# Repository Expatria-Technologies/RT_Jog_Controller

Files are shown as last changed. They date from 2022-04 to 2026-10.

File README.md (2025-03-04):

flag

# Elbows up.

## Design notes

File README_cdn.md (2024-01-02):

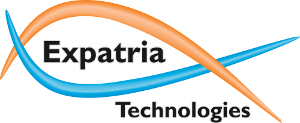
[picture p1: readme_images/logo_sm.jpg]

# Jog2K Jog Controller for GRBLHAL2000 and Flexi-HAL
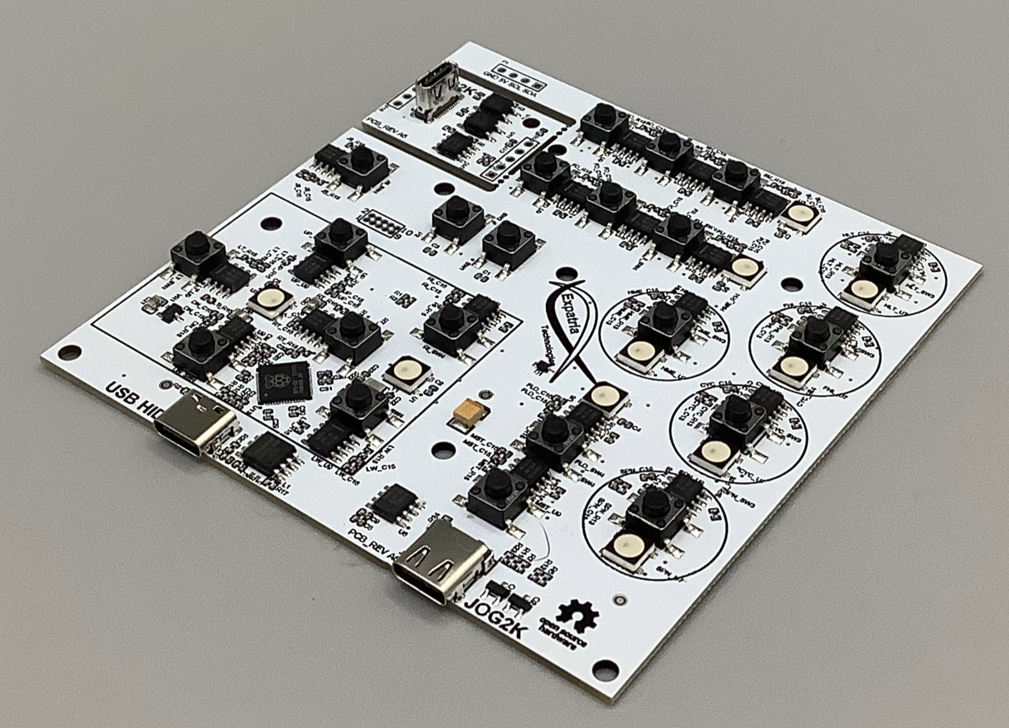
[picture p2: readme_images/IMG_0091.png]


Expatria Technologies jog controller for GRBLHAL2000 and Flexi-HAL boards

Assembled PCBs currently available in our online store:

https://expatria.myshopify.com/products/jog2k-keypad-pendant-pcba

Please consider buying a board to support our open-source designs.

This jog controller was developed for the GRLBHAL20000 and Flexi-HAL boards.  It is designed to be relatively inexpensive and simple to assemble.  It needs minimal manual wiring and leverages 3d printable parts for assembly.  The system consists of a small interface module that is installed on the Real-Time/I2C headers on the Flexi-HAL, plus a simple lighted button keypad that uses a Raspberry Pi Pico to send character commands to GRBLHAL and receive status information.  This pendant relies on the modified I2C Keypad plugin that was extended by Expatria Technologies:

https://github.com/Expatria-Technologies/Plugin_I2C_keypad

The key features of the Jog2K:

1) Immediate access to GRBLHAL jogging functionality and real-time commands
2) DRO with selectable WCS
3) Alternate button function macros

## Jog 2k Slim 1.3
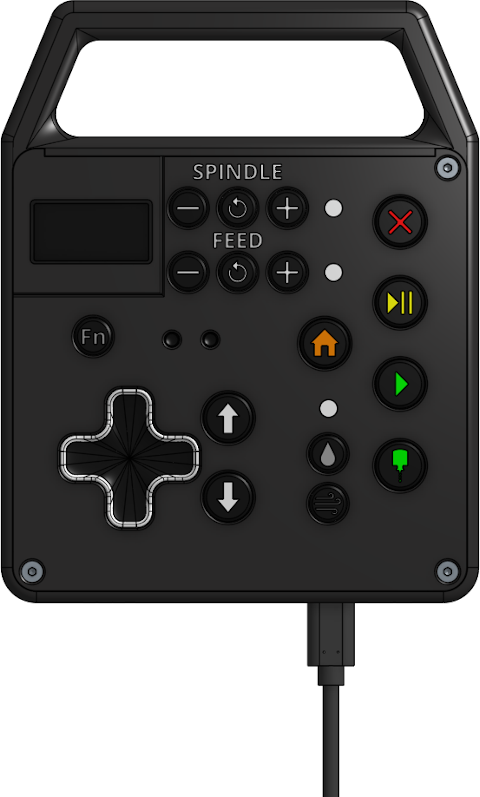
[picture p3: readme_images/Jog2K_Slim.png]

Check out the awesome community mod for the Jog2K using an upgraded 1.3 inch OLED and slimmer enclosure design:

https://github.com/Expatria-Technologies/Mods-Accessories/tree/main/Expatria/Jog2K_Deluxe

## Usage

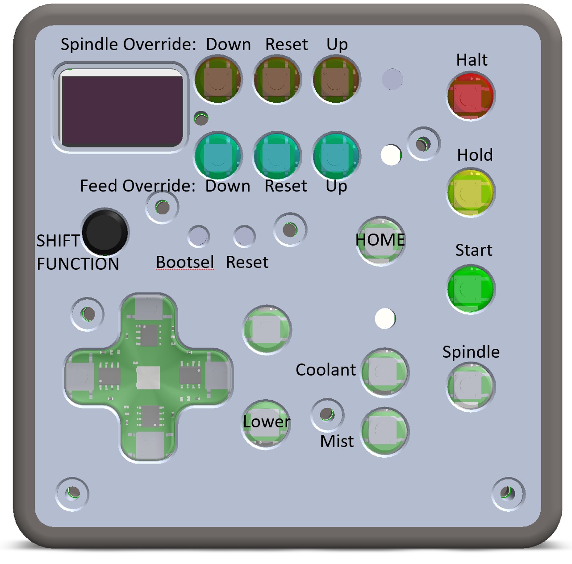
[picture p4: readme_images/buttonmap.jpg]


Many of the buttons on the Jog2K have alternate functions that are accessed via the SHIFT/FUNCTION button.  The XYZ jog buttons give access to the configurable macros.  In the event that a 4th axis is enabled in GRBLHAL, the macro functions of the Z axis buttons are lost and the alternate function for those buttons changes to jogging the A axis.

When used with GRBLHAL, always ensure that "limit jog commands" is true (not like above image) and ensure that the soft limits are properly configured and enabled for your machine.  There are 3 modes:
1) Fast mode continuous jogging.  Machine will jog at the $50 speed until it either travels the $55 fast jog distance or hits the machine limit
2) Slow mode continuous jogging.  Machine will jog at the $51 slower speed until it either travels the $54 slow jog distance or hits the machine limit
3) Step jog mode.  Machine will travel the $53 distance (or to machine limit) and stop.  Usually this step is quite small so the $50 step jog speed isn't relevant, but it is still configurable.

Note that the machine will always stop any move if you lift the button.  This can mean that at large steps with a slow speed it does not complete if you do not hold the button down.

The alternate fuctions for the Mist and Flood buttons control the current jog mode and rate.  The Shift-Mist button toggles between Fast, Slow and step modes (these are configurable in IOSender).  The Shift-Flood button will change the decimal place of the current jog mode.

The Shift-HOME function will toggle between the active WCS: G54, G55 etc.

The Shift-HOLD function will issue a soft reset to the controller.  This is usually used as part of exiting the ESTOP state.

The Shift-RUN function will issue an Unlock command to the controller.  This is usually used as part of exiting the ESTOP state.  Note that this will stop any executing program or motion.

The HALT button has an alternate function which is to flip the OLED screen vertically.  There is no standard orientation for these screens so if yours is upside-down after installation, simply activate the screen flip.  The screen orientation is stored in NVM.  The Jog2K should reset automatically around 2s after the command is issued.

## Macros

It is easiest to configure the macros in IOSender.

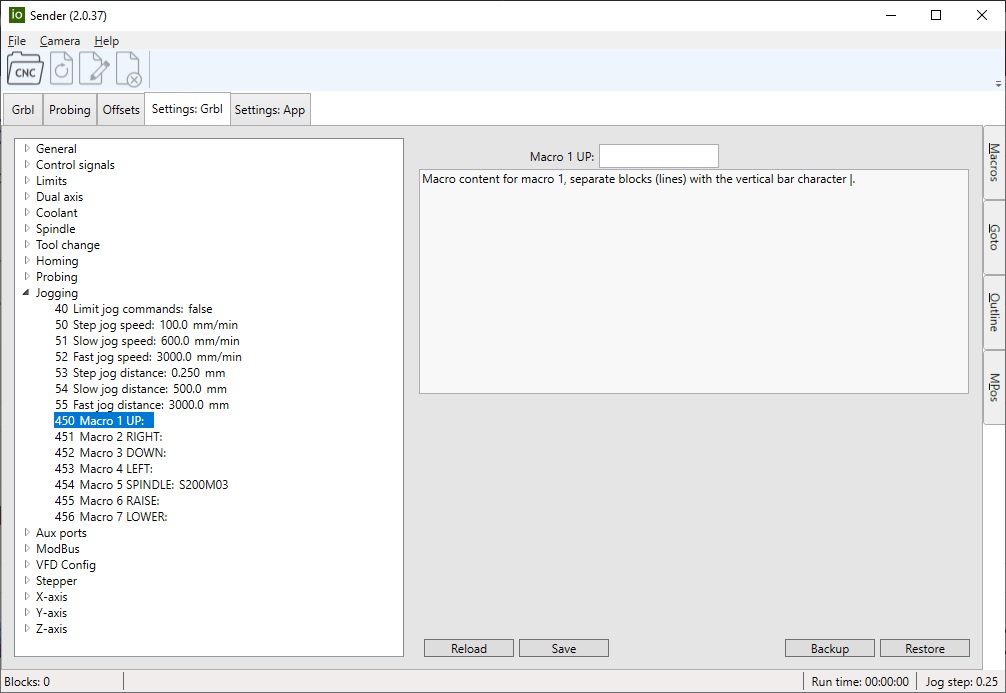
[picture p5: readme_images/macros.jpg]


Each macro is limited to 127 characters.  The macro on the spindle button has a special function that should not be modified.  When the spindle is off, the macro will run and it is intended to start up the spindle at a slow rate (the default value for this macro is 200 RPM, ie the minimum spindle RPM).  When the spindle is running, activating the spindle macro button will send an M5 command to stop the spindle.  The primary use of this functionality is for manual edge-finding.  Assigning other macros to the spindle button is not recommended.

## Cable Interface - 5 Gbps Link Cable Required.

Some pre-release Jog2K systems used RJ45 connections, but all current and future releases will use USB-C connectors on both the Jog2K and the host interface module.  It is cricitical that the correct USBC cable is used.  Many USB-C cables do not have all of the conductors inside and these will not work with the Jog2k.  Always use a cable that is rated for USB-C display (5 Gbps data transfer).  An Oculus Link cable is commonly available and works well.  These cables also have the advantage that they are usually high quality and well shielded.

Please note that on A4 and earlier revisions of the PCB, e-marker cables do not work.

## Assembly

Most users choose to assemble the [Jog2k Deluxe](https://github.com/Expatria-Technologies/Mods-Accessories/blob/main/Expatria/Jog2K_Deluxe) edition of the mechanical design.  These are a series of community updates that increase the polish and legibility of the Jog2K.

Upon receipt of the Jogger, the small interface module should be snapped off from the main PCB if it is not already.  This module is installed on the 5 and 4 pin QWIIC/I2C headers on the GRBLHAL2000 or Flexi-HAL board.  The reason the module is included with the Jog2K is due to part availability challenges.  Different interface designs may be used as parts go in and out of stock, and therefore the interface module is included to ensure compatibility.

In addition to the interface module, the Jog2K requires a 0.96 or 1.3 inch I2C OLED screen.  The current A6 revision of the board uses a discrete RP2040 MCU.  If you wish to use the older board based on the Pi Pico, the A5 files are archived.

Ensure that your oled screen pinout matches the pinout labelled on the jogger PCBA.

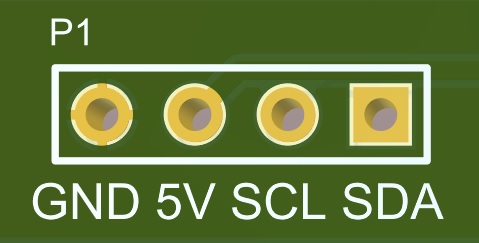
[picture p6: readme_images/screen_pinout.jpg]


Once the PCBA is fully assembled simply print the buttons in clear PETG so that the neopixel functions are visible.  The shift, coolant and override buttons are not backlit and can be printed in black or other suitable colors. For these functions, there are lightpipe models provided.  Finally there are two smaller buttons for BOOTSEL and RESET.

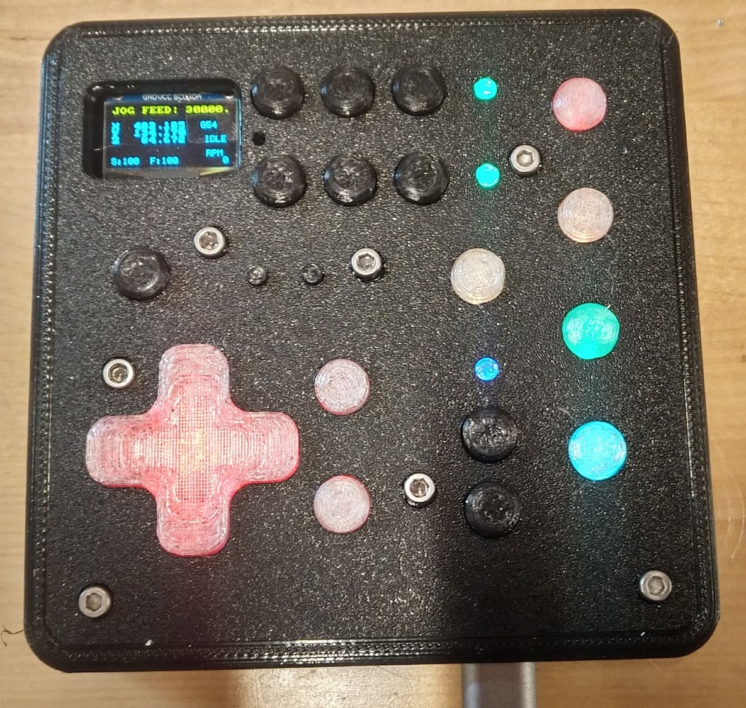
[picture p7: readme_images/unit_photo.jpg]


## Screen
Originally the Jog2K was designed to be used with a 0.96 inch OLED screen that was mounted to the PCB.  However, thanks to the PrintNC community, a new 3d printed enclsoure was developed that allows for the use of a 1.3 inch OLED that is mounted directly the the front panel.  This results in a significantly more readable display and is a massive upgrade over the original screen.  However, this means that some manual assemlby and soldering is required.  Updated STLs are in the Jog2K Deluxe folder in the [Mods & Accessories](https://github.com/Expatria-Technologies/Mods-Accessories/) repo.

### Attributions
This project uses components from the very helpful actiBMS library for JLCPCB SMT parts.

https://github.com/actiBMS/JLCSMT_LIB

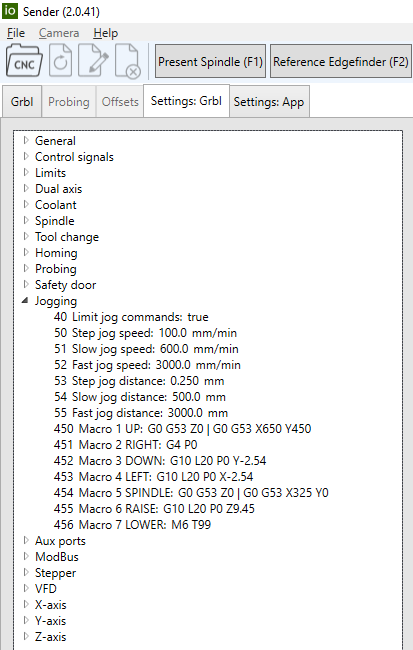
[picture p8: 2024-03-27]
readme_images/more_macros.png

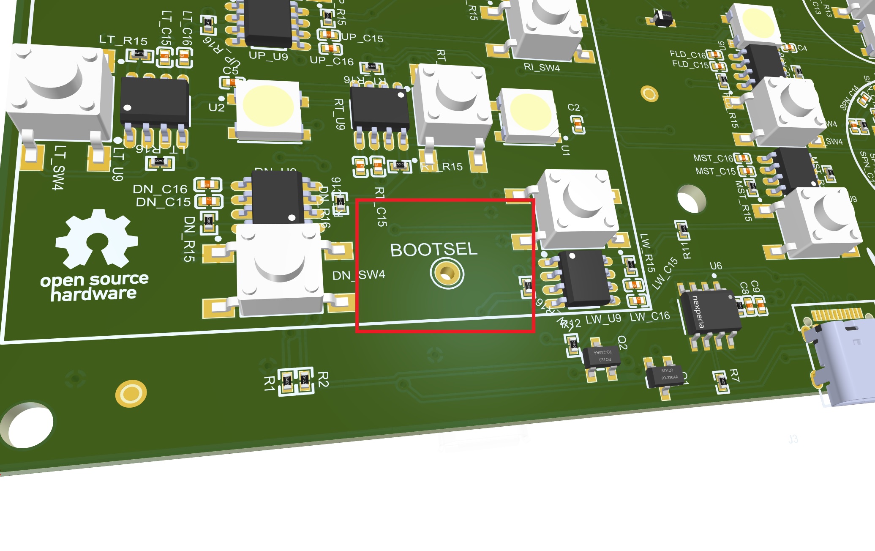
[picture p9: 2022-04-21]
readme_images/bootsel_location.jpg

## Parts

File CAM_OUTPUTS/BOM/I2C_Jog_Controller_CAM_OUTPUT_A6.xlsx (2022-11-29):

Comment | Description | Designator | Footprint | SuppliersPartNumber | Quantity
1.0uF | Chip capacitor | C2, C4, C5, C6, C7, C8, C10, C17, C26, C27, CYC_C12, CYC_C13, CYC_C14, DN_C15, DN_C16, FD_C15, FD_C16, FHL_C12, FHL_C13, FHL_C14, FLD_C15, FLD_C16, FR_C15, FR_C16, FU_C15, FU_C16, HLT_C12, HLT_C13, HLT_C14, HME_C12, HME_C13, HME_C14, JS_C15, JS_C16, LT_C15, LT_C16, LW_C15, LW_C16, MST_C15, MST_C16, RI_C15, RI_C16, RT_C15, RT_C16, SD_C15, SD_C16, SPN_C12, SPN_C13, SPN_C14, SR_C15, SR_C16, SU_C15, SU_C16, UP_C15, UP_C16 | 0402_C | C52923 | 55
100nF | Chip capacitors | C9, C11, C18, C24, C25, C28, C29, C30, C31, C32, C33, C34, C35 | 0402_C | C1525 | 13
4.7uF | Chip capacitor | C19 | 0402_C | C23733 | 1
22uF | Chip capacitors | C20, C21, C36 | 0805_C | C2922481 | 3
10pF | Chip capacitors | C22, C23 | 0402_C | C32949 | 2
100uF | Tantalum capacitor | C37 | CASE-B_3528 | C16133 | 1
33KΩ ±1% | Chip resistor | CYC_R13, DN_R15, FD_R15, FHL_R13, FLD_R15, FR_R15, FU_R15, HLT_R13, HME_R13, JS_R15, LT_R15, LW_R15, MST_R15, RI_R15, RT_R15, SD_R15, SPN_R13, SR_R15, SU_R15, UP_R15 | 0402_R | C25779 | 20
1KΩ ±1% | Chip resistor | CYC_R14, DN_R16, FD_R16, FHL_R14, FLD_R16, FR_R16, FU_R16, HLT_R14, HME_R14, JS_R16, LT_R16, LW_R16, MST_R16, R4, R5, R6, R7, R8, R9, R17, R23, R24, RI_R16, RT_R16, SD_R16, SPN_R14, SR_R16, SU_R16, UP_R16 | 0402_R | C11702 | 29
K2-1102SP-C4SC-04 | Top Actuated 50mA @ 12VDC Round Button SPST 6*6mm Tactile Switches ROHS | CYC_SW3, DN_SW4, FD_SW4, FHL_SW3, FLD_SW4, FR_SW4, FU_SW4, HLT_SW3, HME_SW3, JS_SW4, LT_SW4, LW_SW4, MST_SW4, RI_SW4, RT_SW4, SD_SW4, SPN_SW3, SR_SW4, SU_SW4, SW1, SW2, UP_SW4 | TECO-FSM4JSMATR_V | C127509 | 22
WS2812B-B/W | Intelligent Control LED Integrated Light Source, 3.5 to 5.3 V, -25 to 80 degC, 4-Pin SMD, RoHS, Tape and Reel | CYC_U7, FHL_U7, HLT_U7, HME_U7, SPN_U7, U1, U2, U3, U4, U5 | ADA-RGB-1655_V | C2761795 | 10
NE555DR | 时基集成 | CYC_U8, DN_U9, FD_U9, FHL_U8, FLD_U9, FR_U9, FU_U9, HLT_U8, HME_U8, JS_U9, LT_U9, LW_U9, MST_U9, RI_U9, RT_U9, SD_U9, SPN_U8, SR_U9, SU_U9, UP_U9 | SOIC-8_150mil | C7593 | 20
1N4148WS T4 | 二极管 | D1 | SOD-323 | C2128 | 1
TYPE-C-31-M-12 | USB Connectors 24 Receptacle 1 8.94*7.3mm RoHS | J1 | HRO_TYPE-C-31-M-12 | C165948 | 1
TYPE-C-31-M-04 | CONN RCP USB3.1 TYPEC 24P SMD RA | J3 | USB-C-SMD_TYPE-C-USB-20 | C129018 | 1
GT-USB-7061 | CONN RCP USB3.1 TYPEC 24P SMD VERT | J4 | USB-C-SMD_GT-USB-7061 | C2762983 | 1
W25Q128JVSIQ_TR | Inductor | L1 | SOIC127P780X195-8N | C97521 | 1
MMBT5551 G1 | 三极管 | Q1, Q2 | SOT-23(SOT-23-3) | C2145 | 2
4.7KΩ ±1% | Chip resistor | R1, R2, R3 | 0402_R | C25900 | 3
DNP | Resistor, ±5%, 0.05W | R10 | 0402 |  | 1
10KΩ ±1% | Chip resistor | R11, R12 | 0402_R | C25744 | 2
22Ω ±1% | Chip resistor | R18, R19 | 0402_R | C25092 | 2
5.1KΩ ±1% | Chip resistor | R20, R21 | 0402_R | C25905 | 2
470Ω ±1% | Chip resistor | R22 | 0402_R | C25117 | 1
P82B715TD,112 | IC REDRIVER I2C 1CH 400KHZ 8SO | U6, U10 | FP-SOT96-1-MFG | C2652383 | 2
EL357N(B)(TA)-G | 贴片光耦 | U11, U12 | SOP-4_P2.54 | C6649 | 2
RP2040 | RP2040 First MCU from RPI | U13 | RP2040 | C2040 | 1
XC6206P332MR | 200mA 680mV@(100mA) Fixed 3.3V~3.3V Positive 1 6V SOT-23-3L Linear Voltage Regulators (LDO) ROHS | VR1 | SOT-23-3L | C5446 | 1
YSX321SL | Crystal or Oscillator | Y1 | YSX321SL | C9002 | 1

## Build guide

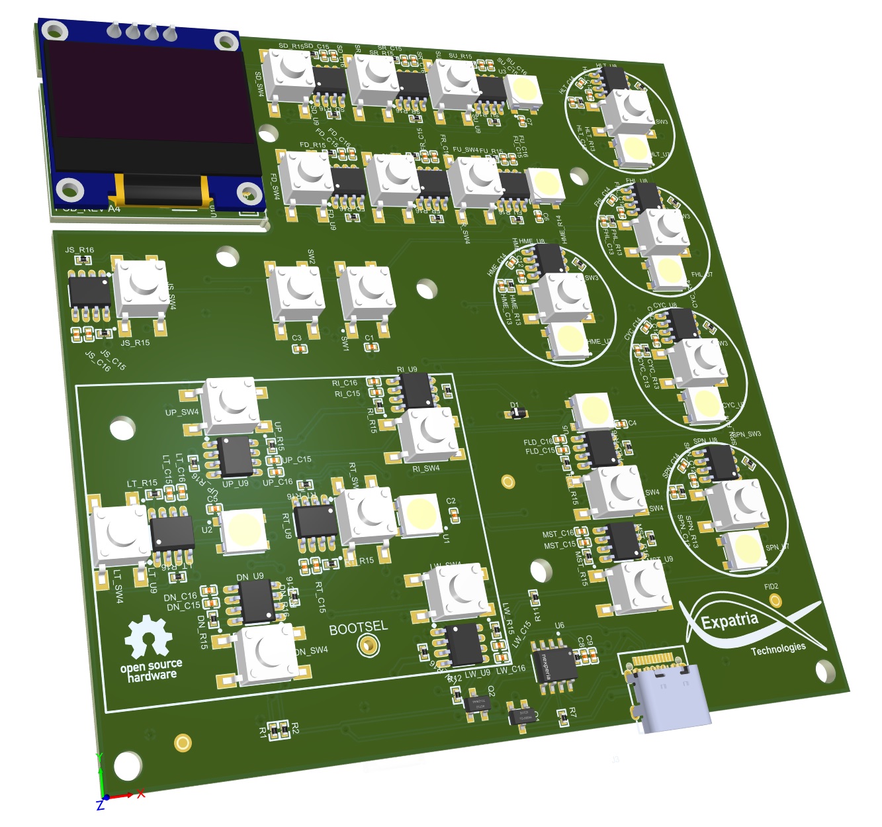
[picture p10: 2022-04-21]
readme_images/screen_install.jpg

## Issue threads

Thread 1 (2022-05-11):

BOM issues on A4 revision prior to commit e533c6e

andrewmarles, 2022-05-11:
There was an issue with the BOM for the early A4 release.  The following parts need to be added:

3 WS2812 LEDs
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

The part is COM-16347 at digikey or C2761795 at LCSC, orientation marked above.

Also need to install Q2 at this location:
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

LCSC C2145 or 1514-CMPT5551TRPBFREECT-ND at Digikey

andrewmarles, 2022-11-17:
None of these early boards are being produced any longer.

Closed 2022-11-17.

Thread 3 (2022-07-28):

Feature Req: Uniquee Jog speed variables for each axis

5ocworkshop, 2022-07-28:
It would be nice to be able to set jog speeds (esp maximum) separately for each axis.  In particular I'm thinking of the case where you want the max jog speed on the Z to be quite a bit lower than the XY.  For example 2000 mm/min, while your XY jog might be 8000/min.  The idea being that you don't want to crash your Z accidentally by jogging at high speed since the physical travel is so short.

At present, I have my Z axis speed limited using the overall travel rate option, but I am realizing this may be contributing to my poor edge finishes when I am milling plywood at high speeds (8000+mm/min) as the optimal Z travel for that XY speed may not be achievable within my travel limit (not sure, just theorizing) - however I don't want to risk jogging the Z at 8000 mm/min.

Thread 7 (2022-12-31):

Bottom Enclosure 1.3 slim.stl is the top instead.

LoganFraser, 2022-12-31:
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

LoganFraser, 2022-12-31:
As above, the BottomEnclosure1.3slim.STL is of the top, not the bottom.

andrewmarles, 2023-01-02:
Fixed.  Thanks very much.

Closed 2023-01-02.

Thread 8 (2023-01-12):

Add "Simplified" sub-directory and its buttons to the Deluxe version's Button sub-directories

R-Ronald, 2023-01-12:
Currently the Deluxe version of the Jog2K uses 9 buttons that are printed in white with black button caps (along with many other buttons that are not relevant to this request).

I have an alternative set of buttons that use icons designed to be "colored in" using a dark Ultra Fine Point Sharpie. The buttons are simpler and less difficult to print, don't require assembly, and provide better contrast/legibility.

I have 6 STL files for 3d printing the 9 required buttons. I also have a readme.txt that provides instructions for substituting these buttons for the baseline version and a readme.pdf that includes a picture. All 8 of these files are designed to live a single sub- directory with the tentative name of "Simplified" alongside the White, Black and Clear sub-directories.

Github doesn't seem to allow STL uploads for a pull request, but I have them ready to go. Here are the two readme files:
[readme.txt](https://github.com/Expatria-Technologies/RT_Jog_Controller/files/10404879/readme.txt)
[readme.pdf](https://github.com/Expatria-Technologies/RT_Jog_Controller/files/10404880/readme.pdf)

andrewmarles, 2023-08-10:
Talking to mikem, it sounds like this got merged into the mods repo.  Cheers.

Closed 2023-08-10.

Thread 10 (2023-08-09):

RT_Jog_Controller not working

zab-ig, 2023-08-09:
Good afternoon.
I assembled the controller and I have some problems. After the firmware of the controller, the LEDs light up in white and the inscription "GRBLHALL I2C JOGGER" appears on the screen. After that, the screen goes blank and nothing else happens, the LEDs continue to glow white.
Tell me what's the problem?

jaymis, 2023-08-09:
I think you might need to provide some more details @zab-ig
What Controller are you plugging your Jogger into (Flexi-HAL or GRBLHAL2000)? What cable are you using? What firmware version is running on the Jogger and the Controller?

zab-ig, 2023-08-09:
I use GRBLGRBLHAL2000 and LAN cable 1 m long. Version firmware Jogger 1.0.2, GRBLHAL2000 V.230529.
If you connect an oscilloscope to the i2с jogger bus, then there are signals on the SСL and SDA lines.
If you supply power to the jogger and do not connect it to the GRBL controller, how should it behave? In my case, the LEDs light up white, an inscription appears on the "GRBLHALL I2C JOGGER" screen, and then the screen goes blank.

jaymis, 2023-08-09:
That's correct behaviour for the jogger if it's powered but not connected to a controller. It needs to communicate with the controller to do anything else.

andrewmarles, 2023-08-09:
You need to use exactly the linked branch of the keypad plug-in:

https://github.com/Expatria-Technologies/Plugin_I2C_keypad

This is linked in the read me.  The pre built firmware uses that branch.

https://github.com/Expatria-Technologies/iMXRT1062/releases/tag/v1.05

zab-ig, 2023-09-01:
Thank you. Everything is working.

zab-ig, 2023-09-01:
A new problem has arisen.
 If I flash GRBL2000 firmware 1.05, then the Jog_Controller works. But in 1.05 EEPROM is not activated. I downloaded the source https://github.com/Expatria-Technologies/iMXRT1062. In my_machine.h I have activated all the necessary plugins including the KEYPAD_ENABLE. The firmware compiles successfully. After the firmware, the Jog_Controller does not work correctly. The screen displays the coordinates at the moment the Jog_Controller is connected to the GRBL2000, the Jog_Controller does not respond to buttons, the coordinates on the screen do not change. The iosender program lists all enabled plugins except for the keyboard:
%
; grblHAL
; 1.1f.20230129
; [OPT:VNMSL,35,1024,3,0]
; [NEWOPT:ENUMS,RT+,ES,REBOOT,TC,SED,RTC,ETH,ODO]
; [FIRMWARE:grblHAL]
; [NVS STORAGE:*FRAM]
; [DRIVER:iMXRT1062]
; [DRIVER VERSION:230125]
; [DRIVER OPTIONS:USB.2]
; [BOARD:GRBLHAL2000 - PRINTNC]
; [AUX IO:4,1,0,0]
; [IP:]
; [PLUGIN:MODBUS v0.14]
; [PLUGIN:MODVFD v0.03]
; [SPINDLE:PWM]
; [PLUGIN:RGB Indicator Lights v1.0]
; [PLUGIN:ODOMETERS v0.02]

andrewmarles, 2023-09-01:
Did you install the fram yourself?  That part isn’t on the BoM.  You will need to sort that out if you are using something other than what we built.  The eeprom isn’t used on our builds because it is too small to hold all of the config data from later grblhal versions.

Closed 2024-01-01.

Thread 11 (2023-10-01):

Adding MPG

JasonTitcomb, 2023-10-01:
Would it be possible to add an MPG rotary encoder somehow?

andrewmarles, 2024-01-18:
Probably need to define somehow.  Anything is possible with enough time and effort.

Jog3K is in development:
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

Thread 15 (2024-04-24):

Upside down display.

hambudi, 2024-04-24:
I assembled the RT Jog Controller, with the 2k Deluxe enclosure. I attached the LCD screen (upside down as per the instructions on github).

Now the text on the display is upside down, how do I flip the display orientation?
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

andrewmarles, 2024-04-24:
https://github.com/Expatria-Technologies/RT_Jog_Controller?tab=readme-ov-file#usage

`The HALT button has an alternate function which is to flip the OLED screen vertically. There is no standard orientation for these screens so if yours is upside-down after installation, simply activate the screen flip. The screen orientation is stored in NVM. The Jog2K should reset automatically around 2s after the command is issued.`

Closed 2024-04-24.

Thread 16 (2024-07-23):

Integer overflow on display if feed override set in excess of 255

engigeer, 2024-07-23:
Came across this minor display bug when testing the latest beta release of the flexi firmware which seems to be configured to allow for a max feedrate override higher than the default of 200 (set via a flat in the platformio.ini).

Override value is passed to the jog controller as uint8 so values higher than 255 lead to integer overflow and erroneous values displayed on Jogger screen. No obvious impact on actual override values since these are handled by the flexi.

One solution would be to limit the max override value to 250% (no code changes required for the jogger FW but could benefit from a core edit to check configured value and prevent larger entries). Alternatively, changing to uint16 datatype should also resolve the overflow and would only require updates to the jogger FW and keypad plugin.

https://github.com/Expatria-Technologies/RT_Jog_Controller/blob/a9cda99eecc3abf62a47653f67417424420bdd1f/FW/i2c_responder/i2c_jogger.h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

andrewmarles, 2024-07-23:
This *should* be addressed in Jog3K stuff which would be back-ported to jog2k.  I do want to support the extended range of overrides in GRBLHAL.

Closed 2024-11-11.

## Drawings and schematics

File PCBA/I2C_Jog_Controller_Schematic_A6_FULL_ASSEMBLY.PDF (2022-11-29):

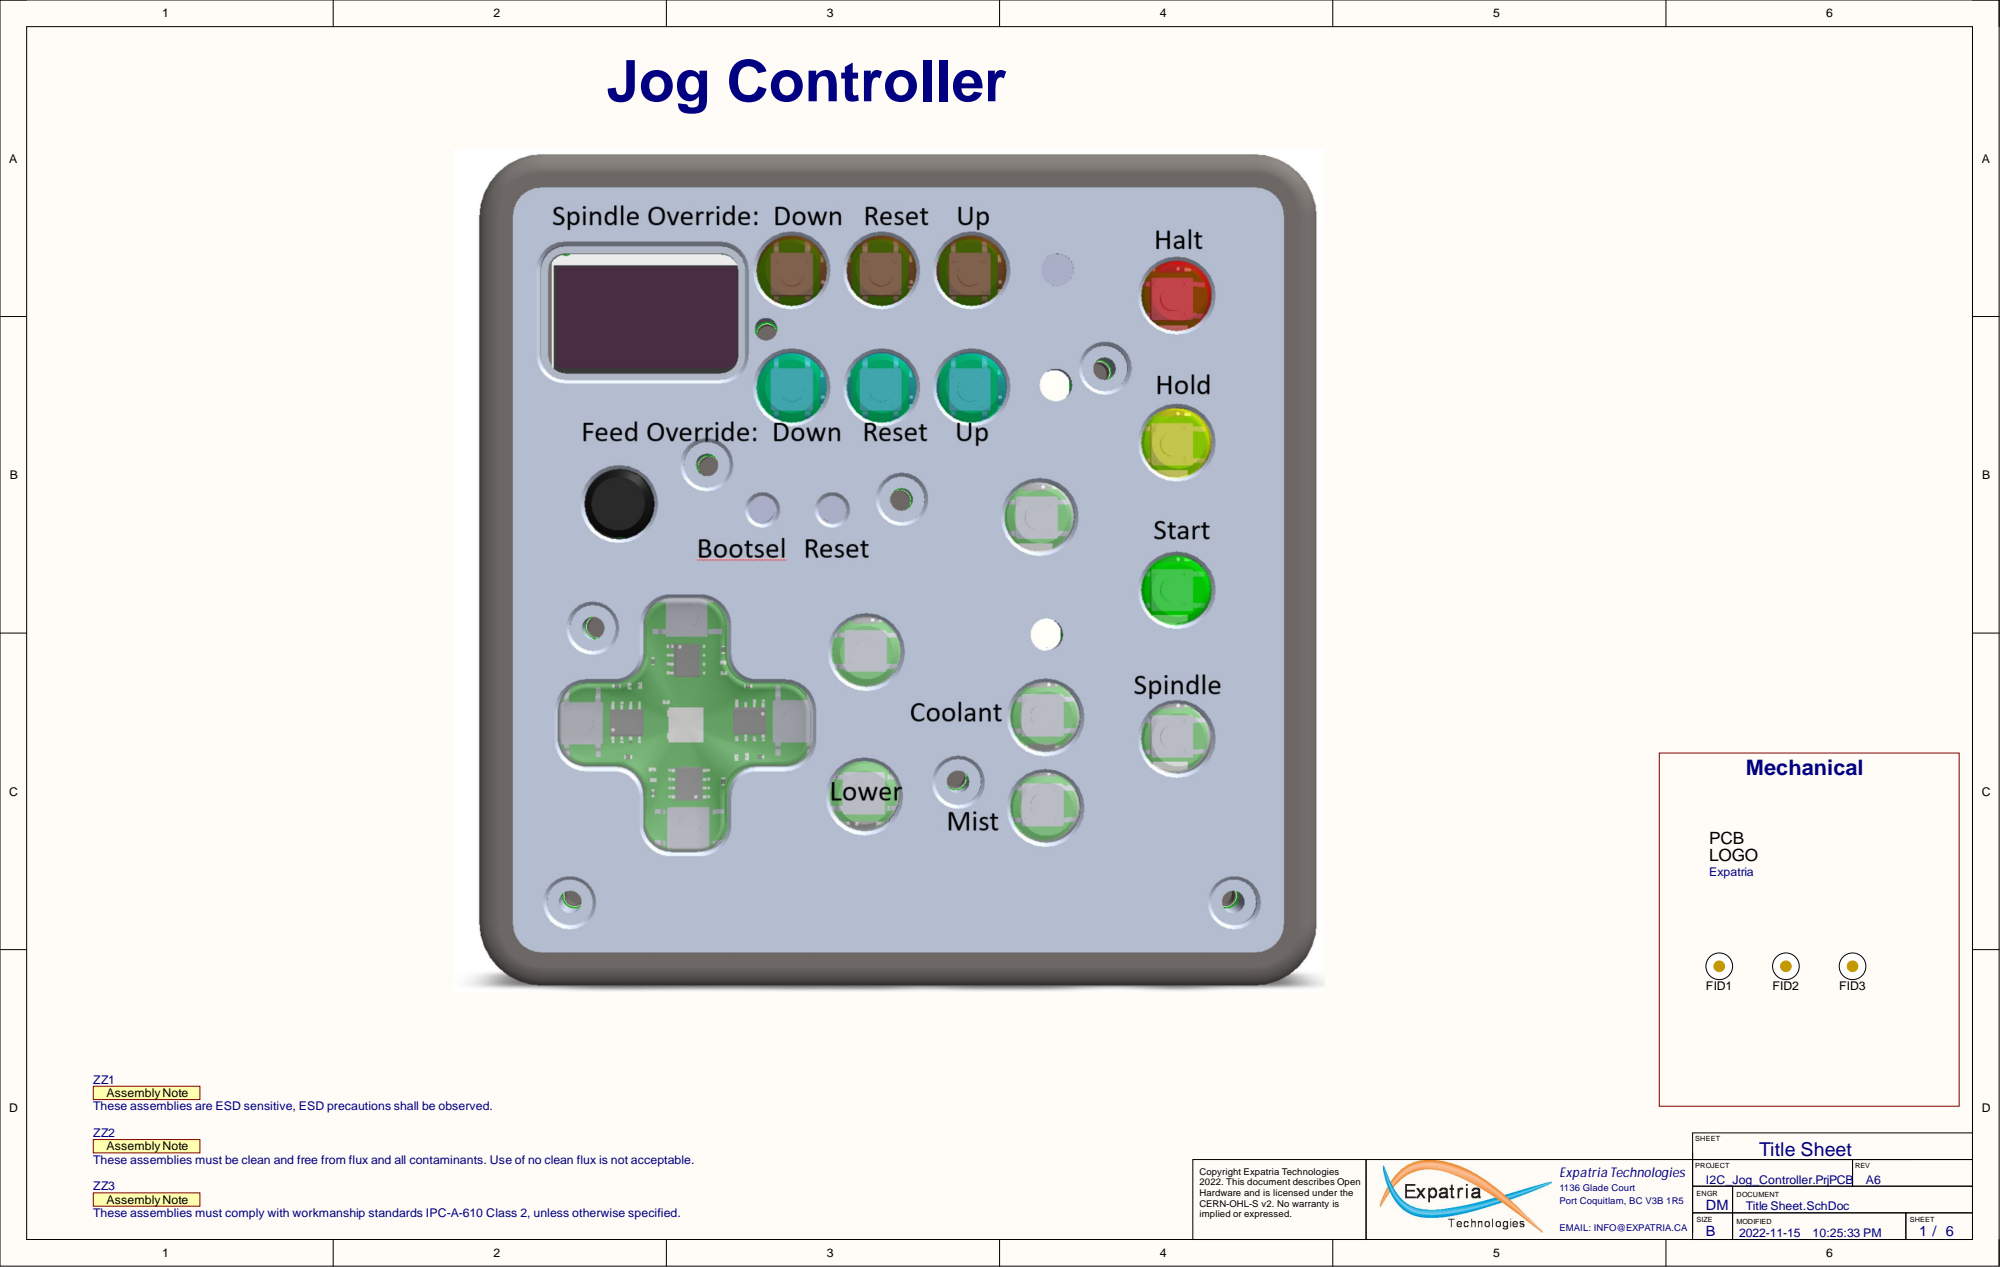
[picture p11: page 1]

Assembly Note
These assemblies are ESD sensitive, ESD precautions shall be observed.

These assemblies must be clean and free from flux and all contaminants. Use of no clean flux is not acceptable.

Copyright Expatria Technologies 2022. This document describes Open Hardware and is licensed under the CERN-OHL-S v2. No warranty is implied or expressed. | | PROJECT I2C_Jog_Controller.PrjPCB | REV A6

These assemblies must comply with workmanship standards IPC-A-610 Class 2, unless otherwise specified.

ENGR DM | DOCUMENT Title Sheet.SchDoc

SIZE B | MODIFIED 2022-11-15 10:25:33 PM | SHEET

EMAIL: INFO@EXPATRIA.CA

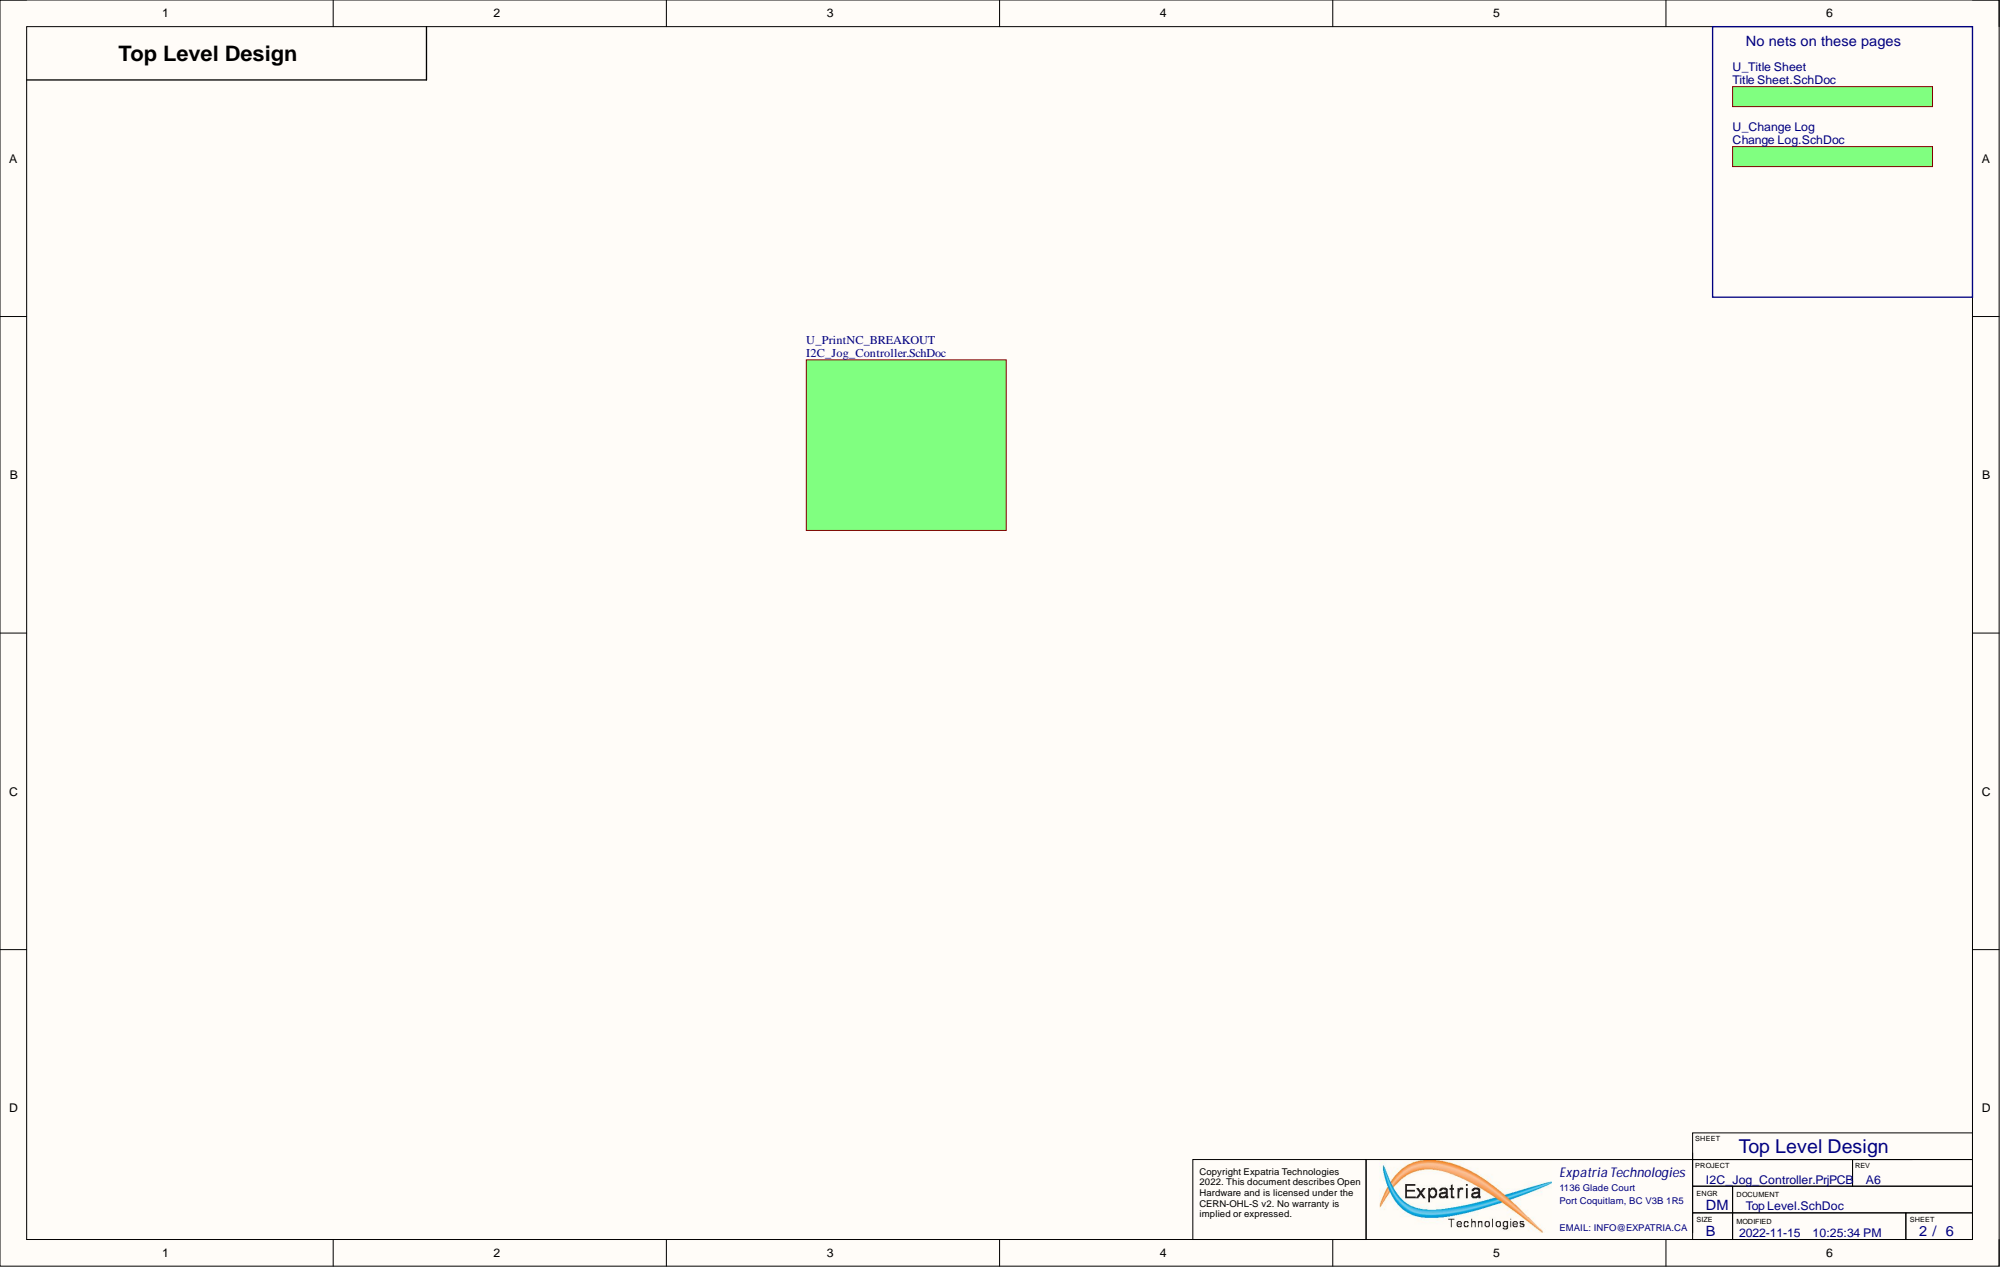
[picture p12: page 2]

No nets on these pages

DM | Top Level.SchDoc

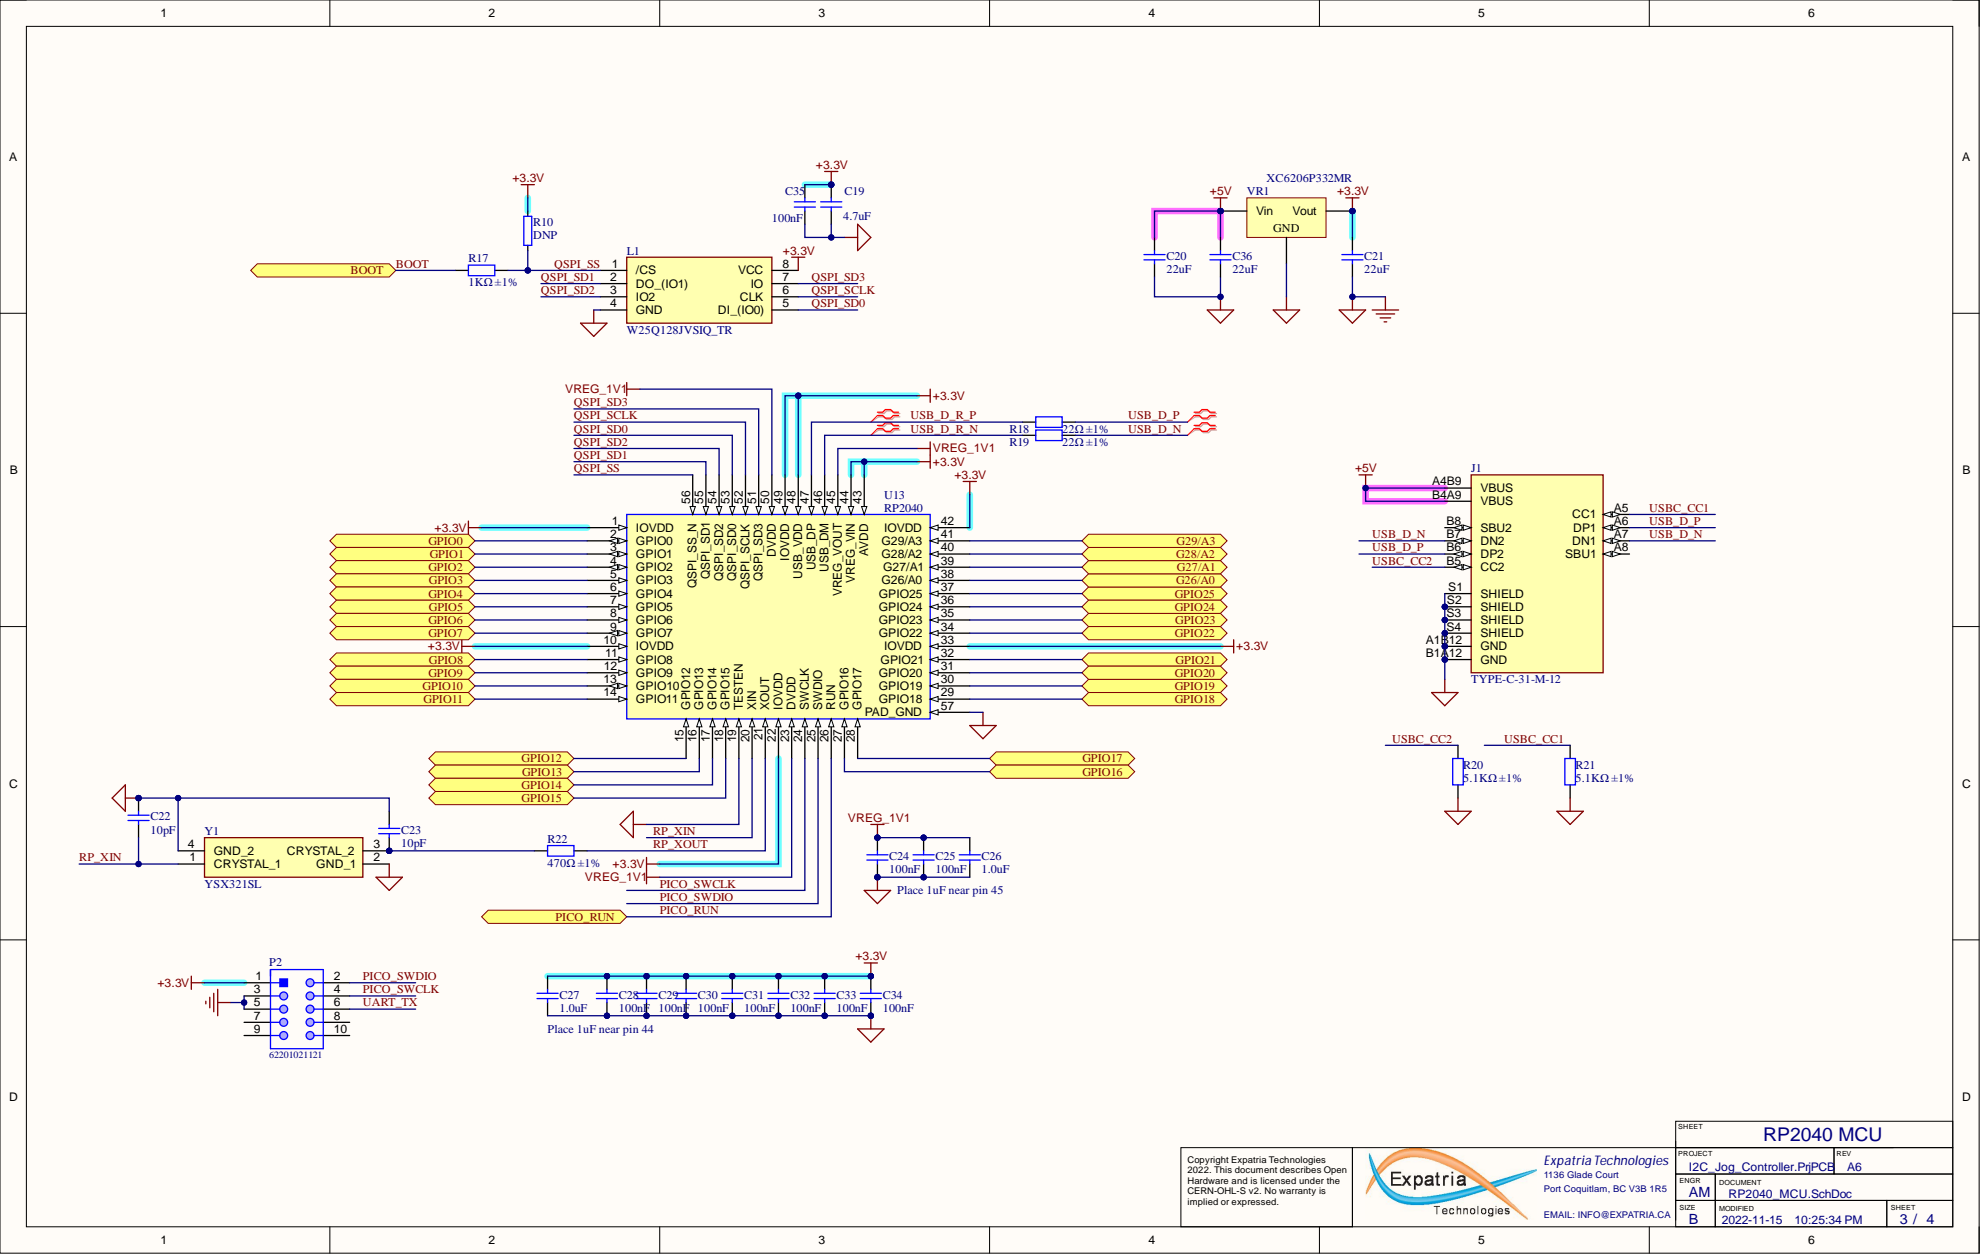
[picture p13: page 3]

QSPI_SD2
QSPI_SD1
QSPI_SS

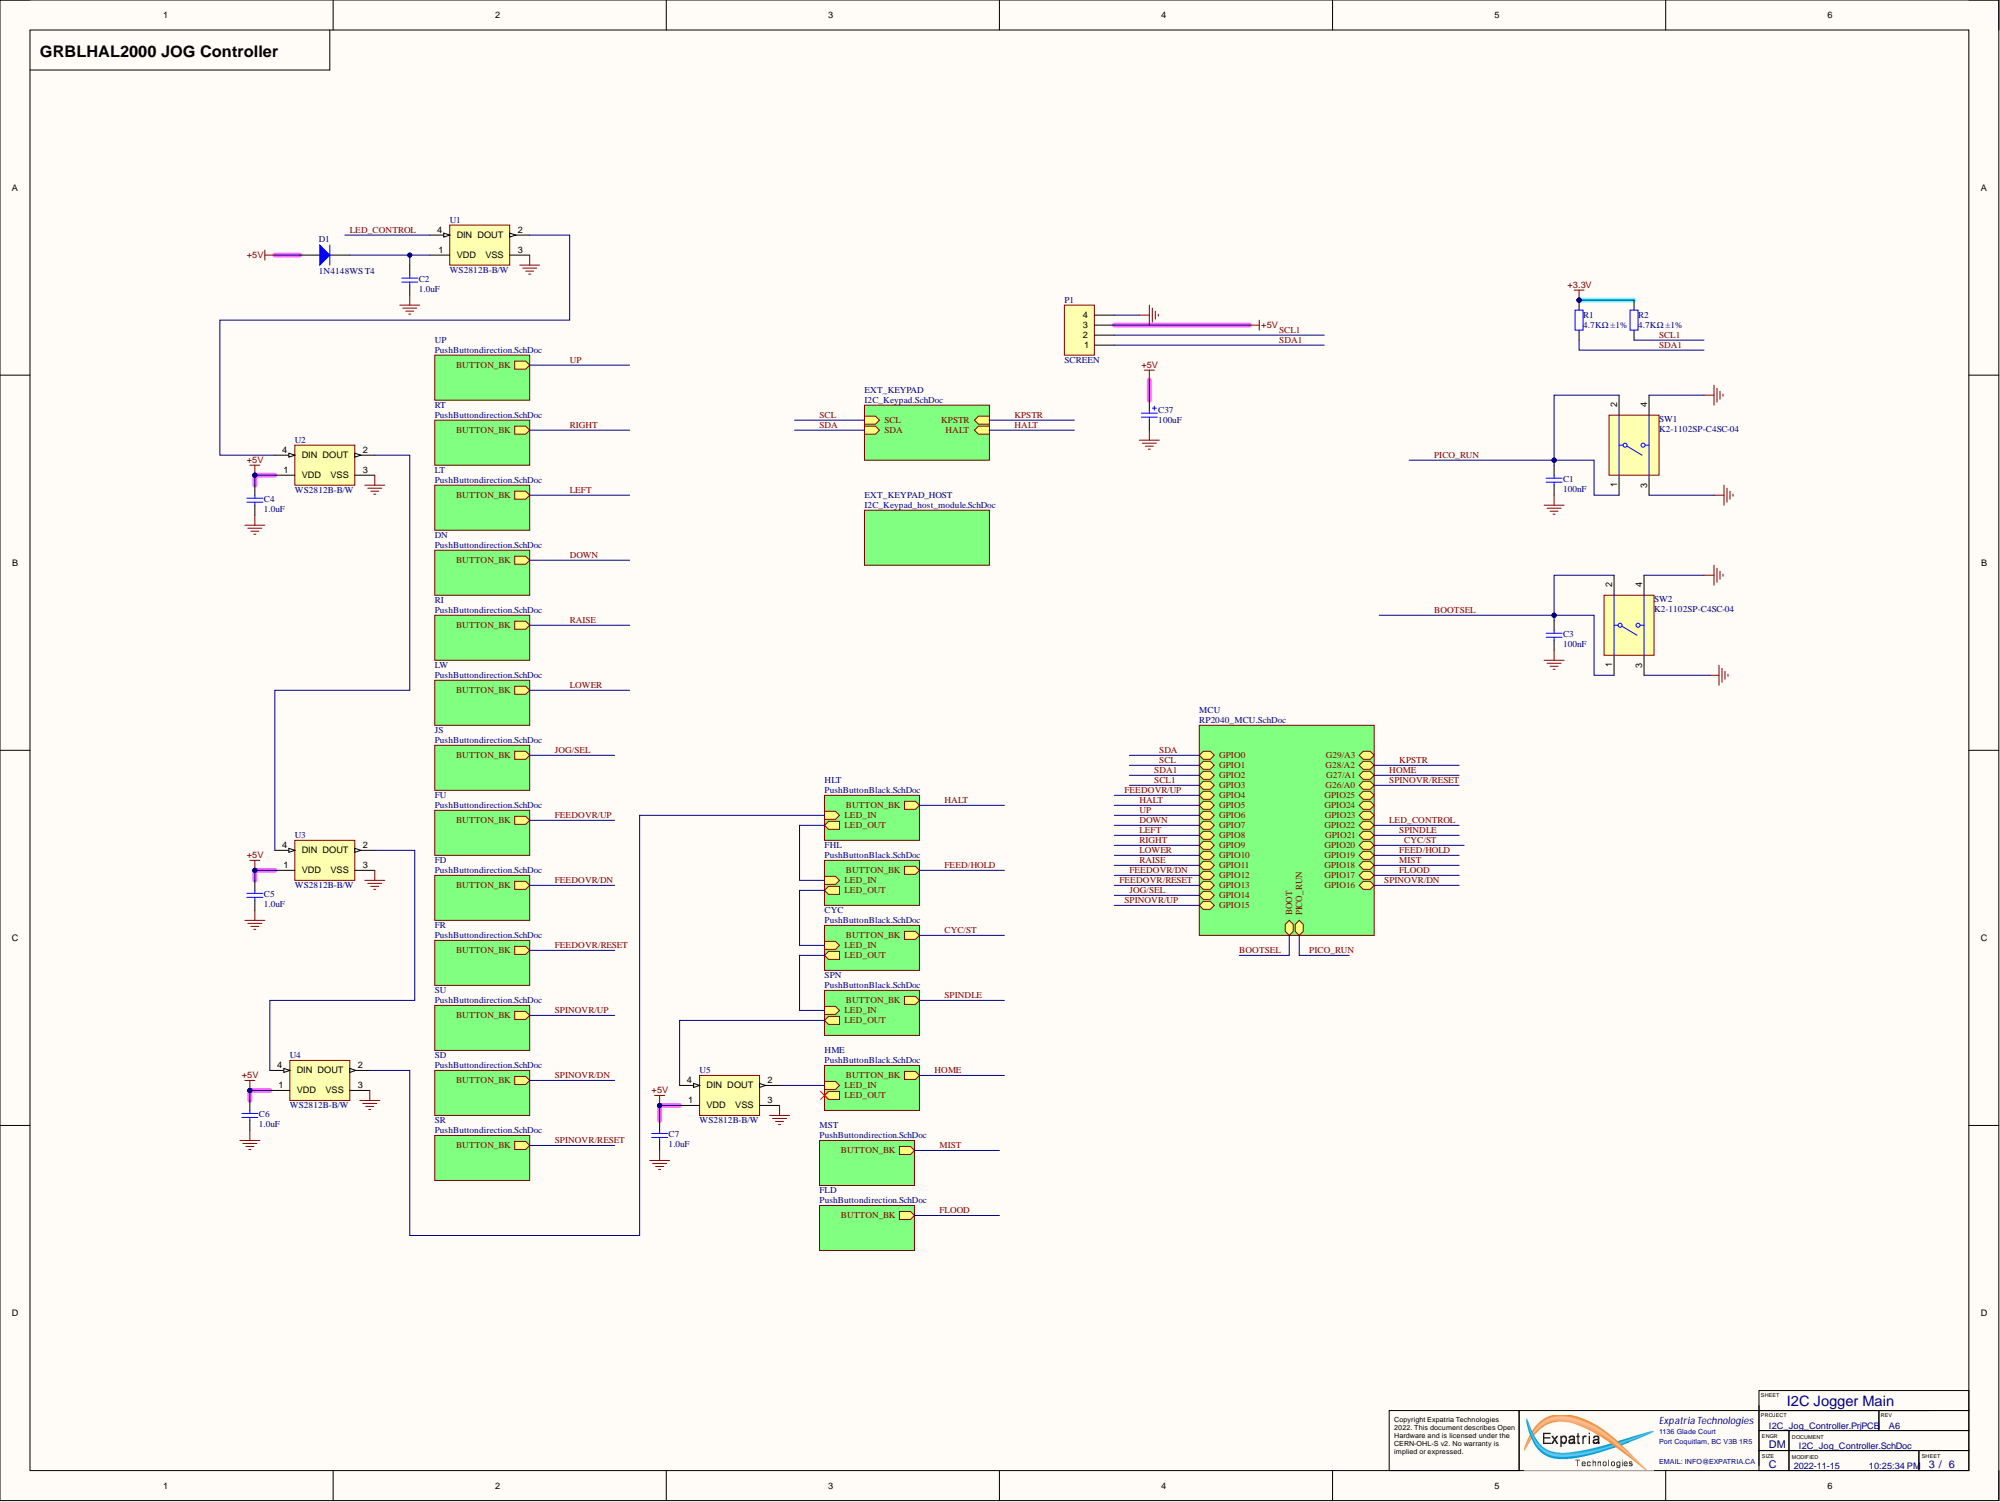
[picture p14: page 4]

Hardware a n d i s l i c e n s e d u n d er th e CERN-OHL-S v 2. No warra nty i s i m p l i e d or e x pre s s e d . | | P R OJE C T I2C_Jog_Controller . P rj P C | R E V

B Copyright Expatria Technologies 2022. This document describes Open

E N G R DM | D O C U M E N T I2C_Jog_Controller . S c h D o c

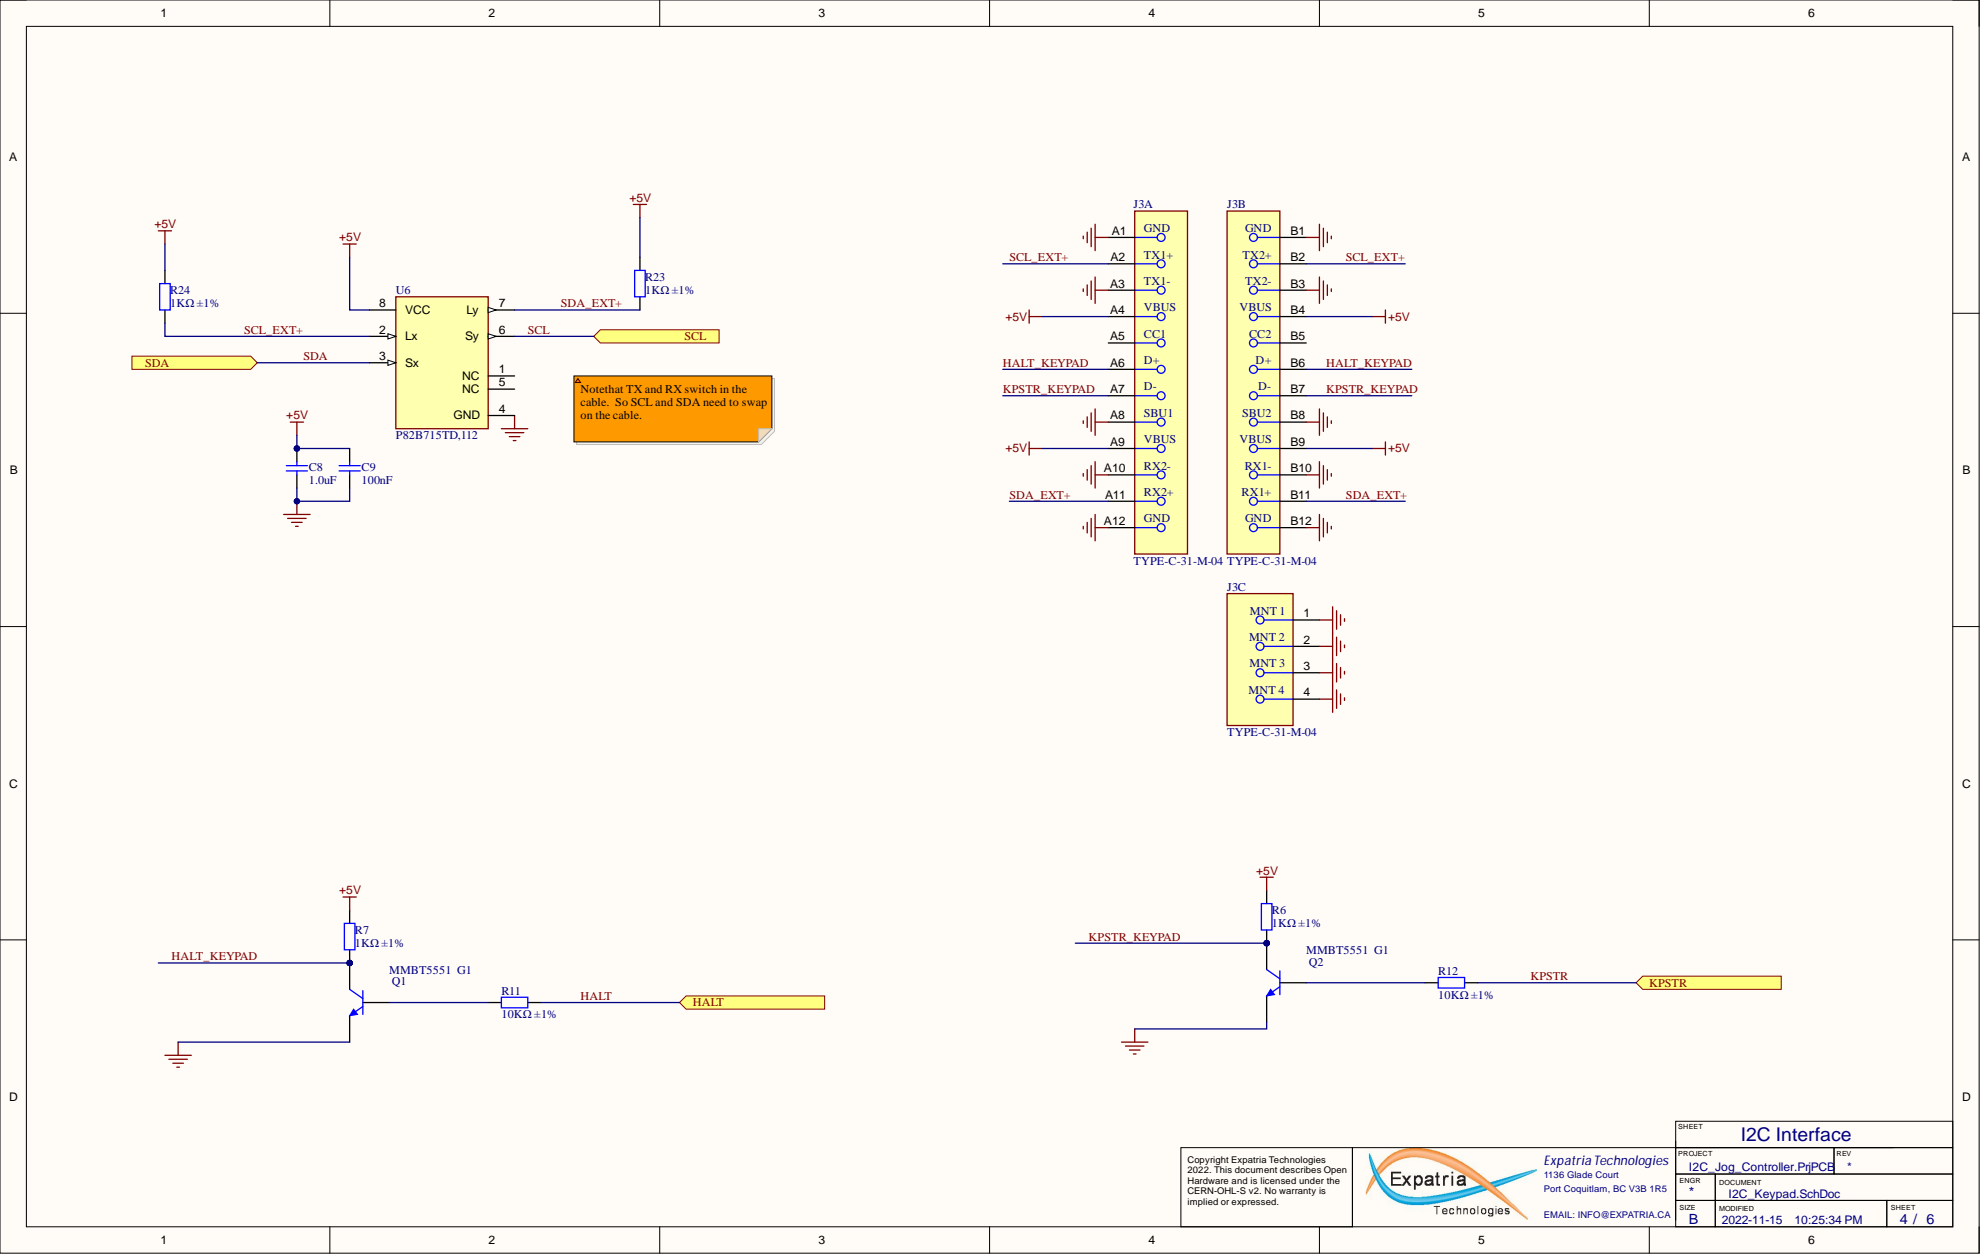
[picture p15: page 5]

Notethat TX and RX switch in the
cable. So SCL and SDA need to swap
on the cable.

* | I2C_Keypad.SchDoc

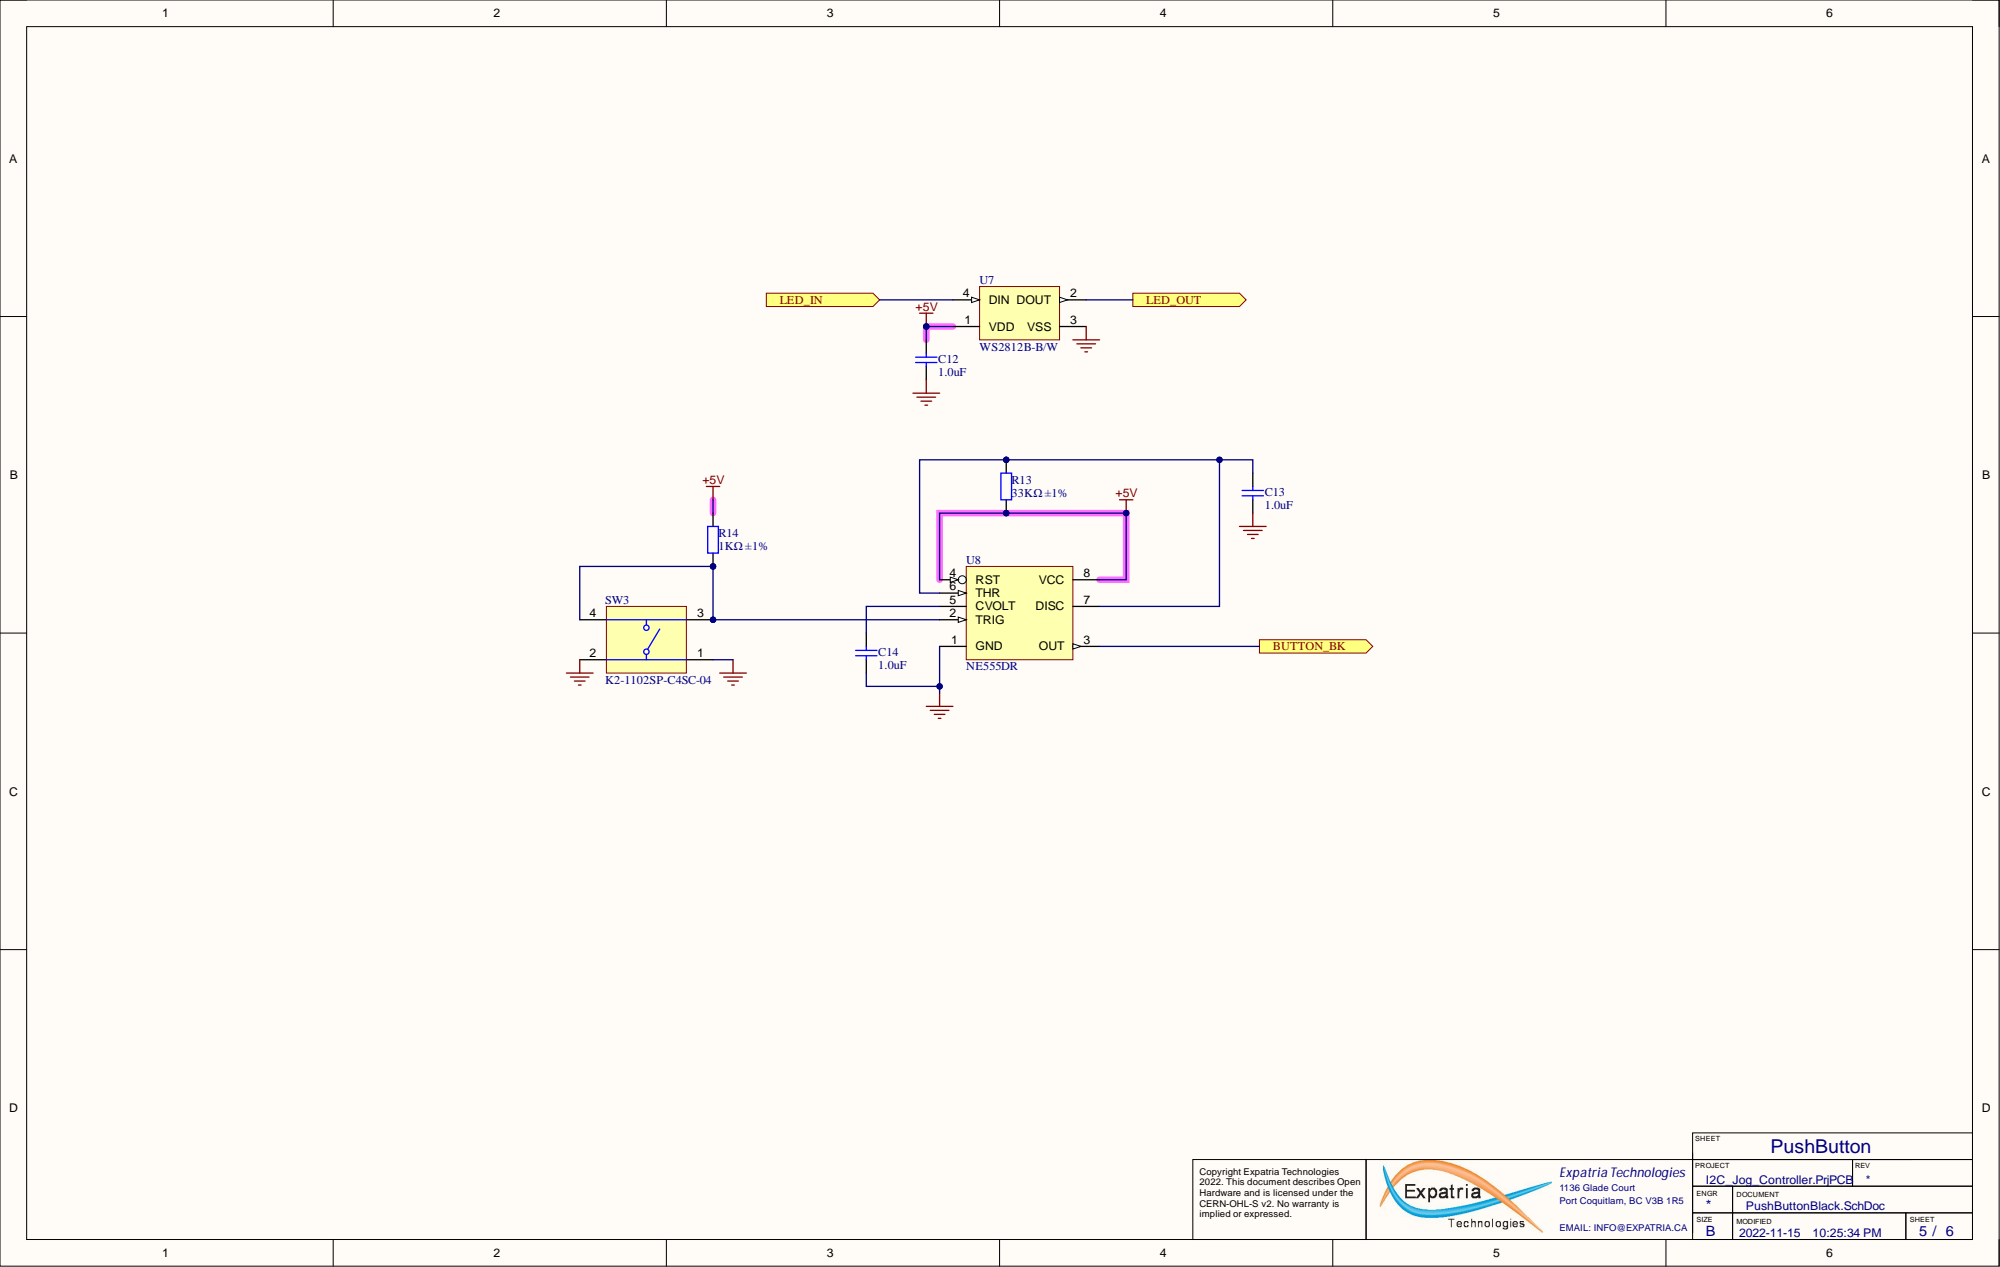
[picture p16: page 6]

TRIG 2

GND 1

* | PushButtonBlack.SchDoc

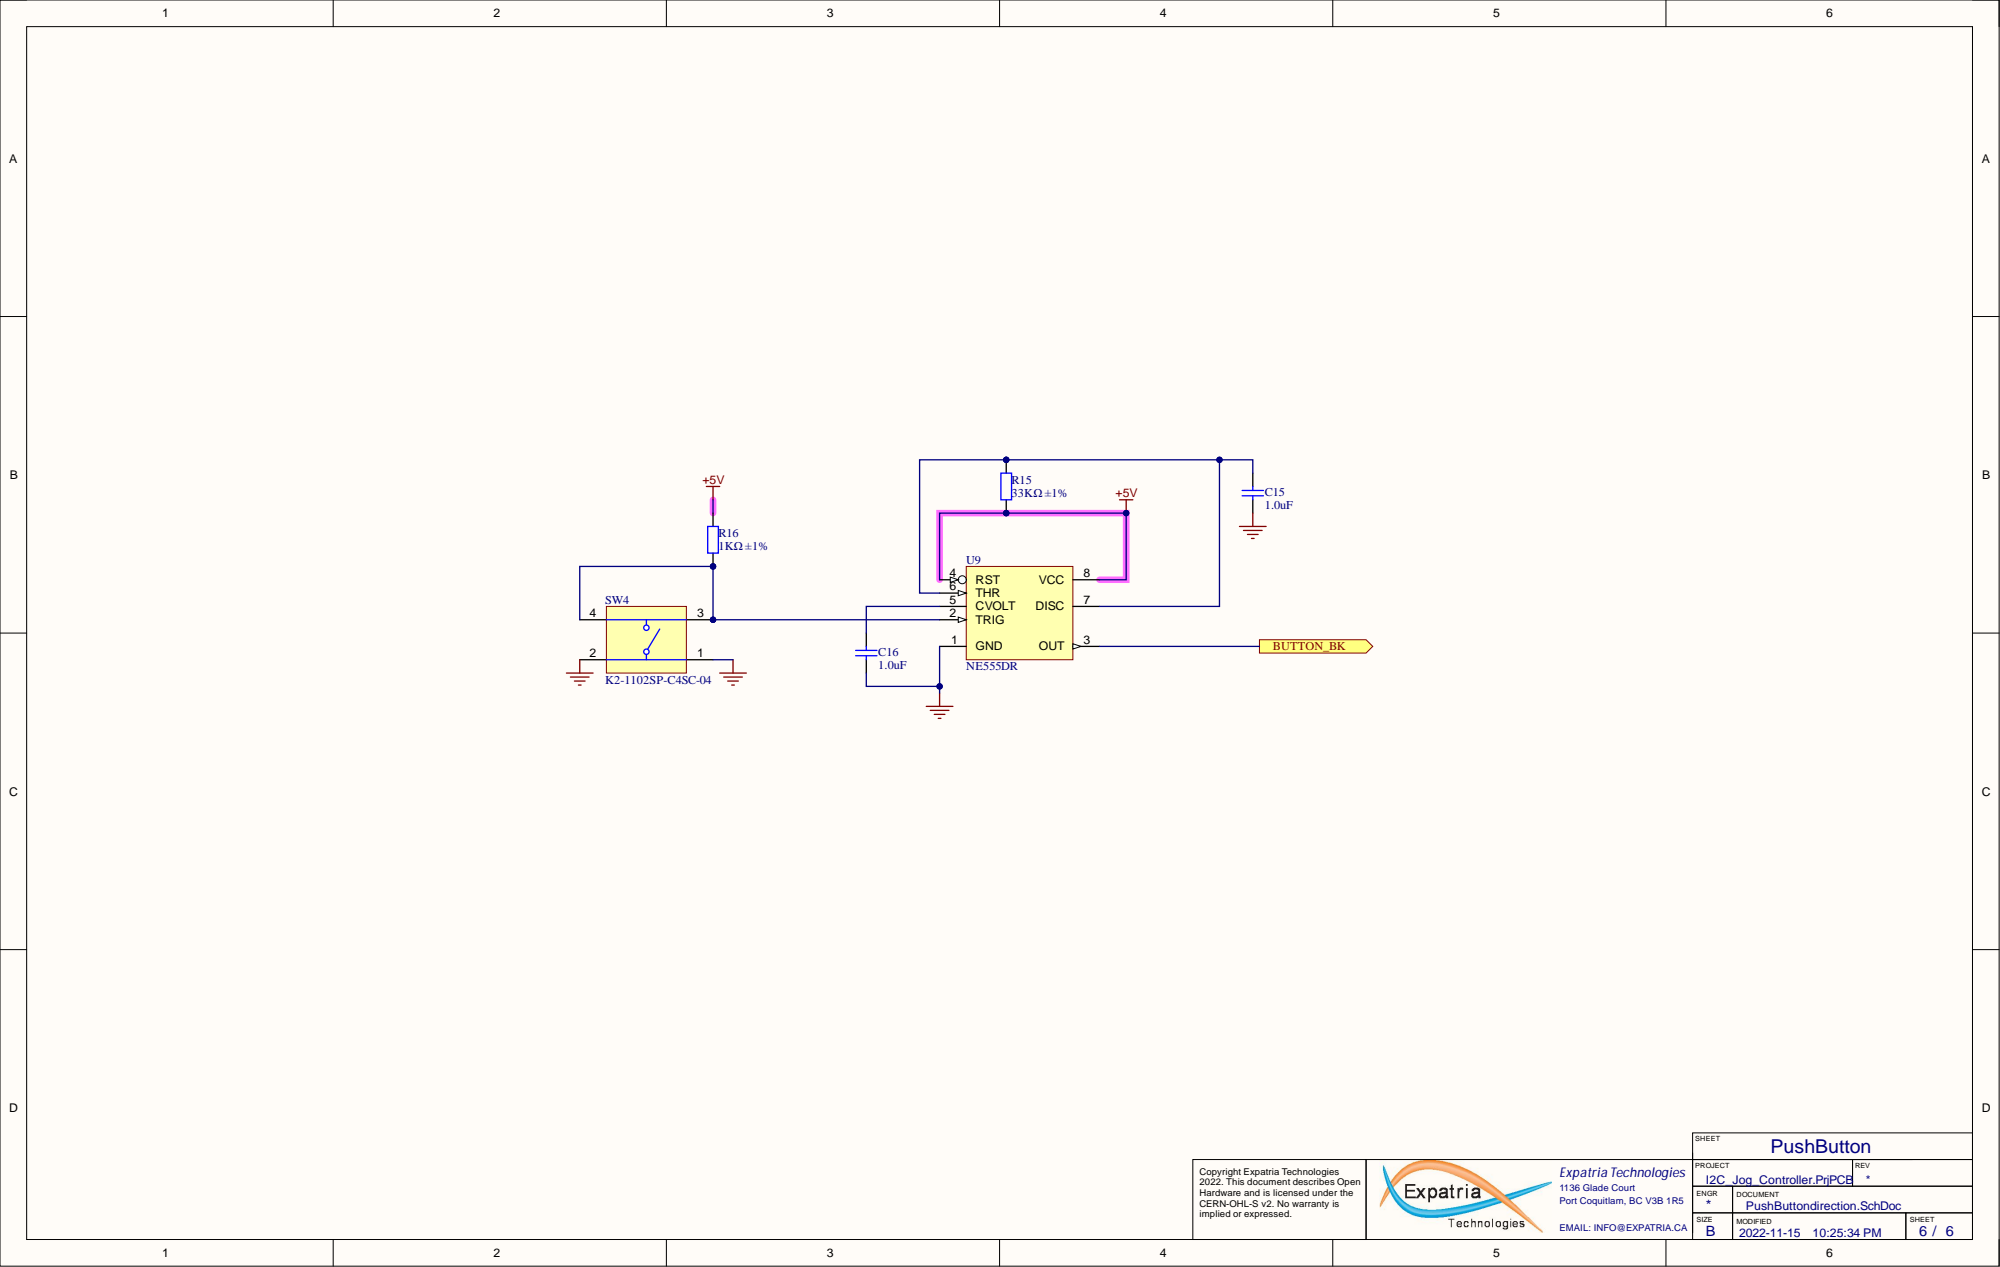
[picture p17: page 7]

Co p yri g ht Ex p atri a Te c h n o l o g i e s 2. Th i s d o c u m e nt d e s cri b e s O p e n Hardware a n d i s l i c e n s e d u n d er th e CERN-OHL-S v 2. No warra nty i s i m p l i e d or e x pre s s e d . | | P R OJE C T I2C_Jog_Controller . P rj P C | R E V *

E N G R * | D O C U M E N T PushBut tondirec tion. S c h D o c

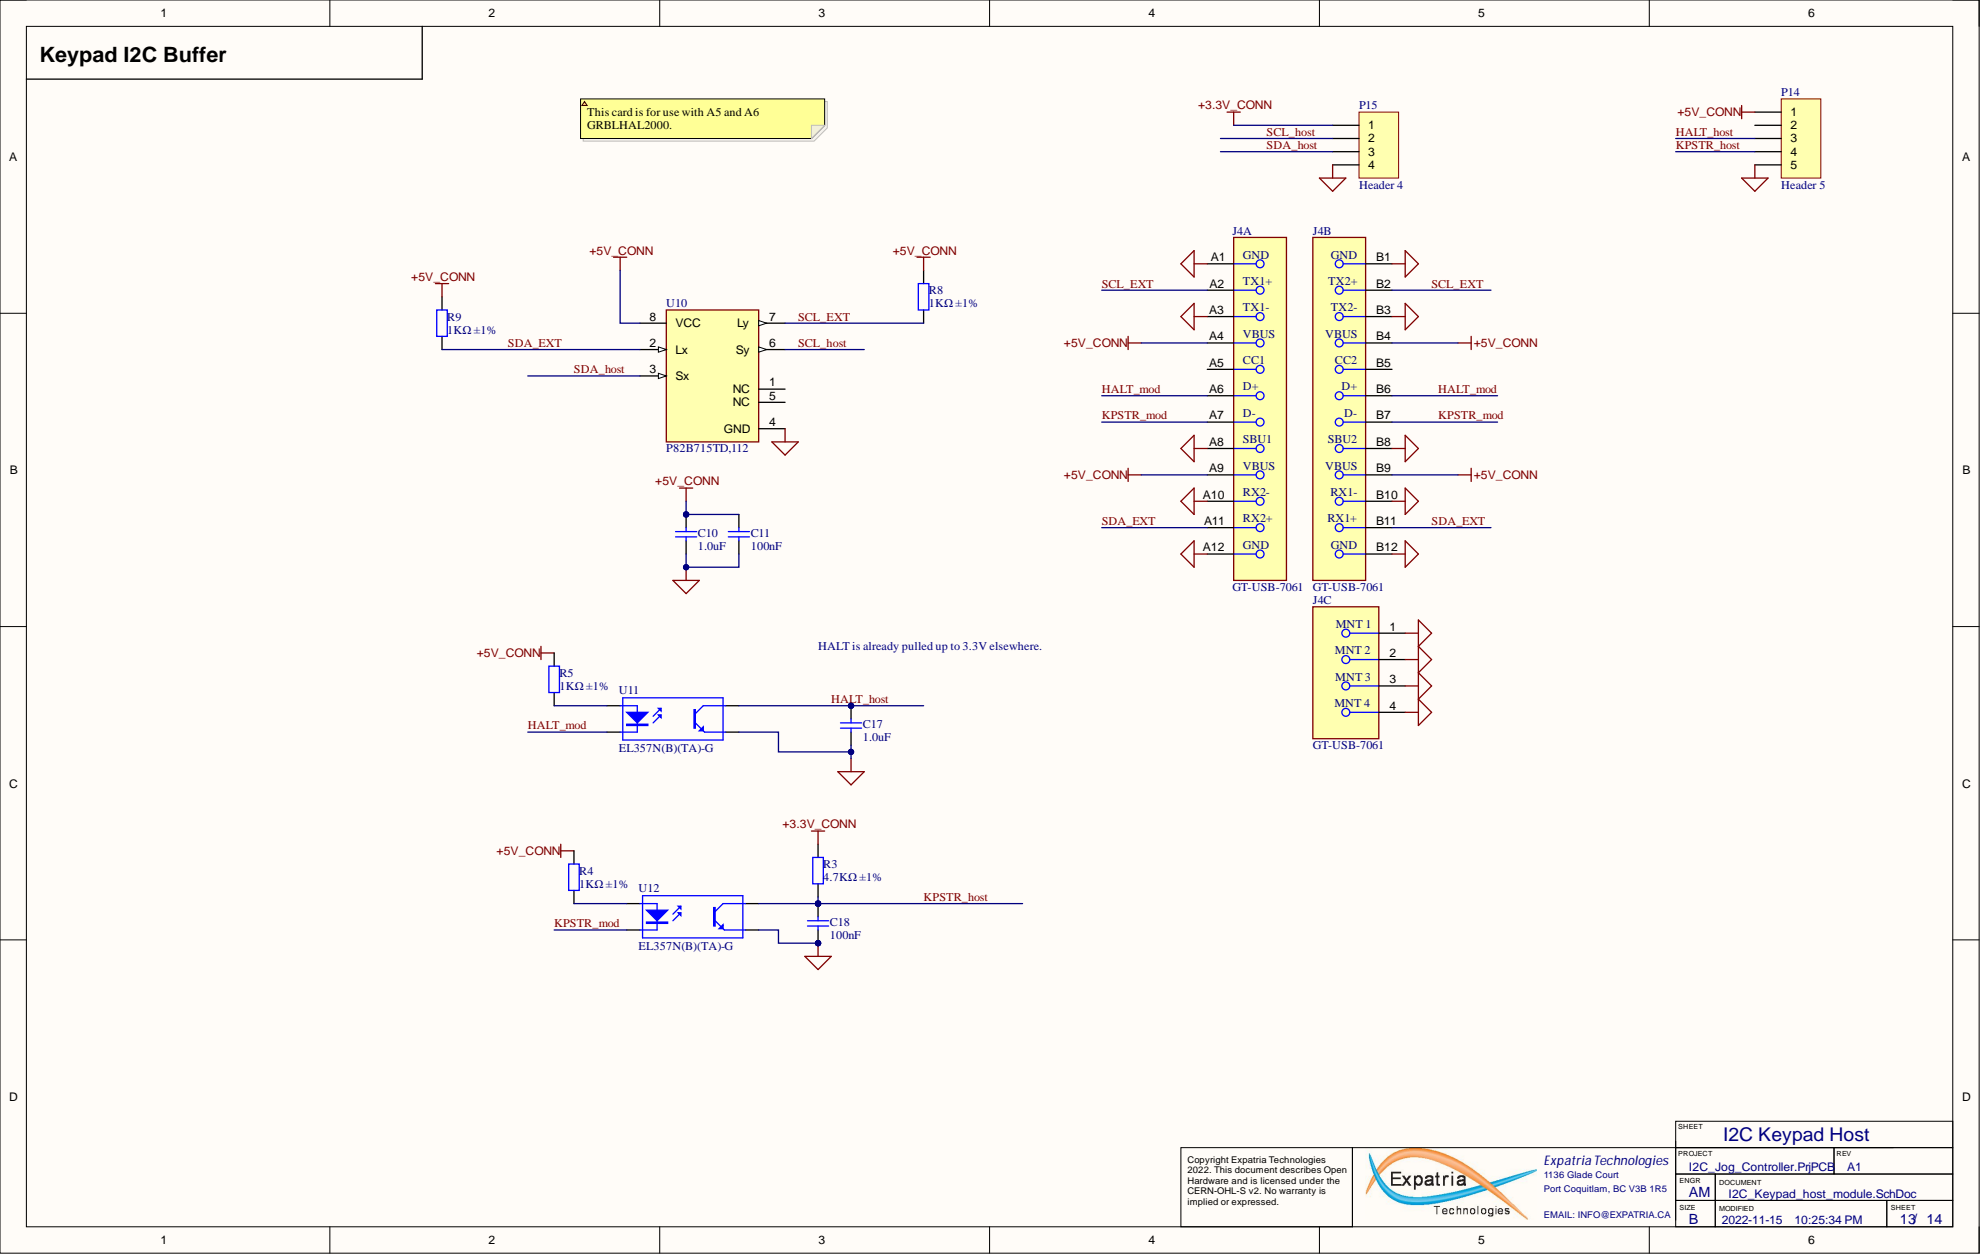
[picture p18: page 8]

This card is for use with A5 and A6
GRBLHAL2000.

HALT is already pulled up to 3.3V elsewhere.

AM | I2C_Keypad_host_module.SchDoc

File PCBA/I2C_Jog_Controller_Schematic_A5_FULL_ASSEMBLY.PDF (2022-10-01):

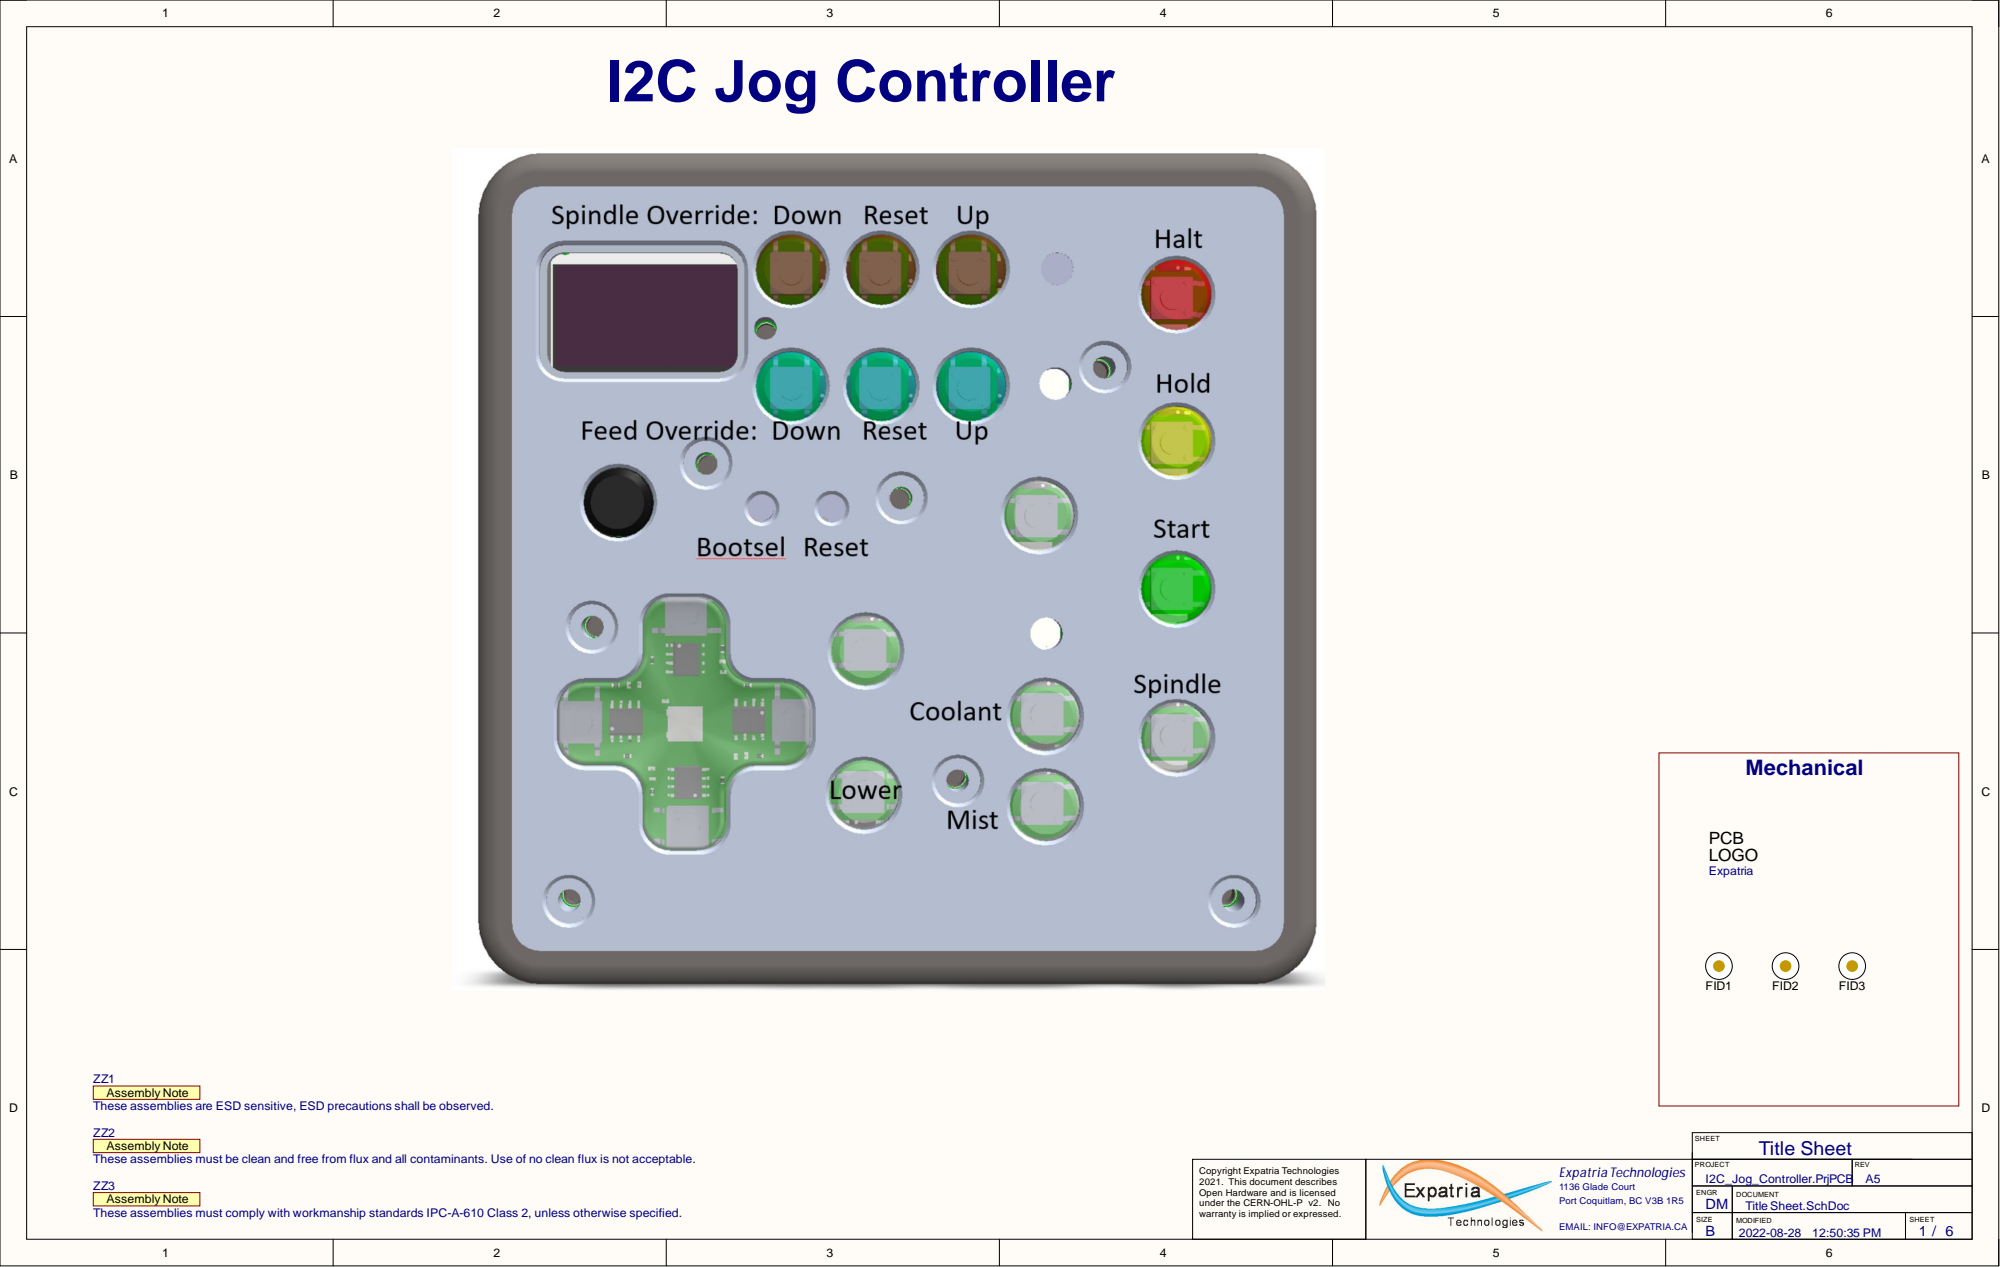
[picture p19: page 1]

Assembly Note
These assemblies are ESD sensitive, ESD precautions shall be observed.

These assemblies must be clean and free from flux and all contaminants. Use of no clean flux is not acceptable.

Copyright Expatria Technologies 2021. This document describes Open Hardware and is licensed under the CERN-OHL-P v2. No warranty is implied or expressed. | | PROJECT I2C_Jog_Controller.PrjPCB | REV A5

These assemblies must comply with workmanship standards IPC-A-610 Class 2, unless otherwise specified.

ENGR DM | DOCUMENT Title Sheet.SchDoc

SIZE B | MODIFIED 2022-08-28 12:50:35 PM | SHEET

EMAIL: INFO@EXPATRIA.CA

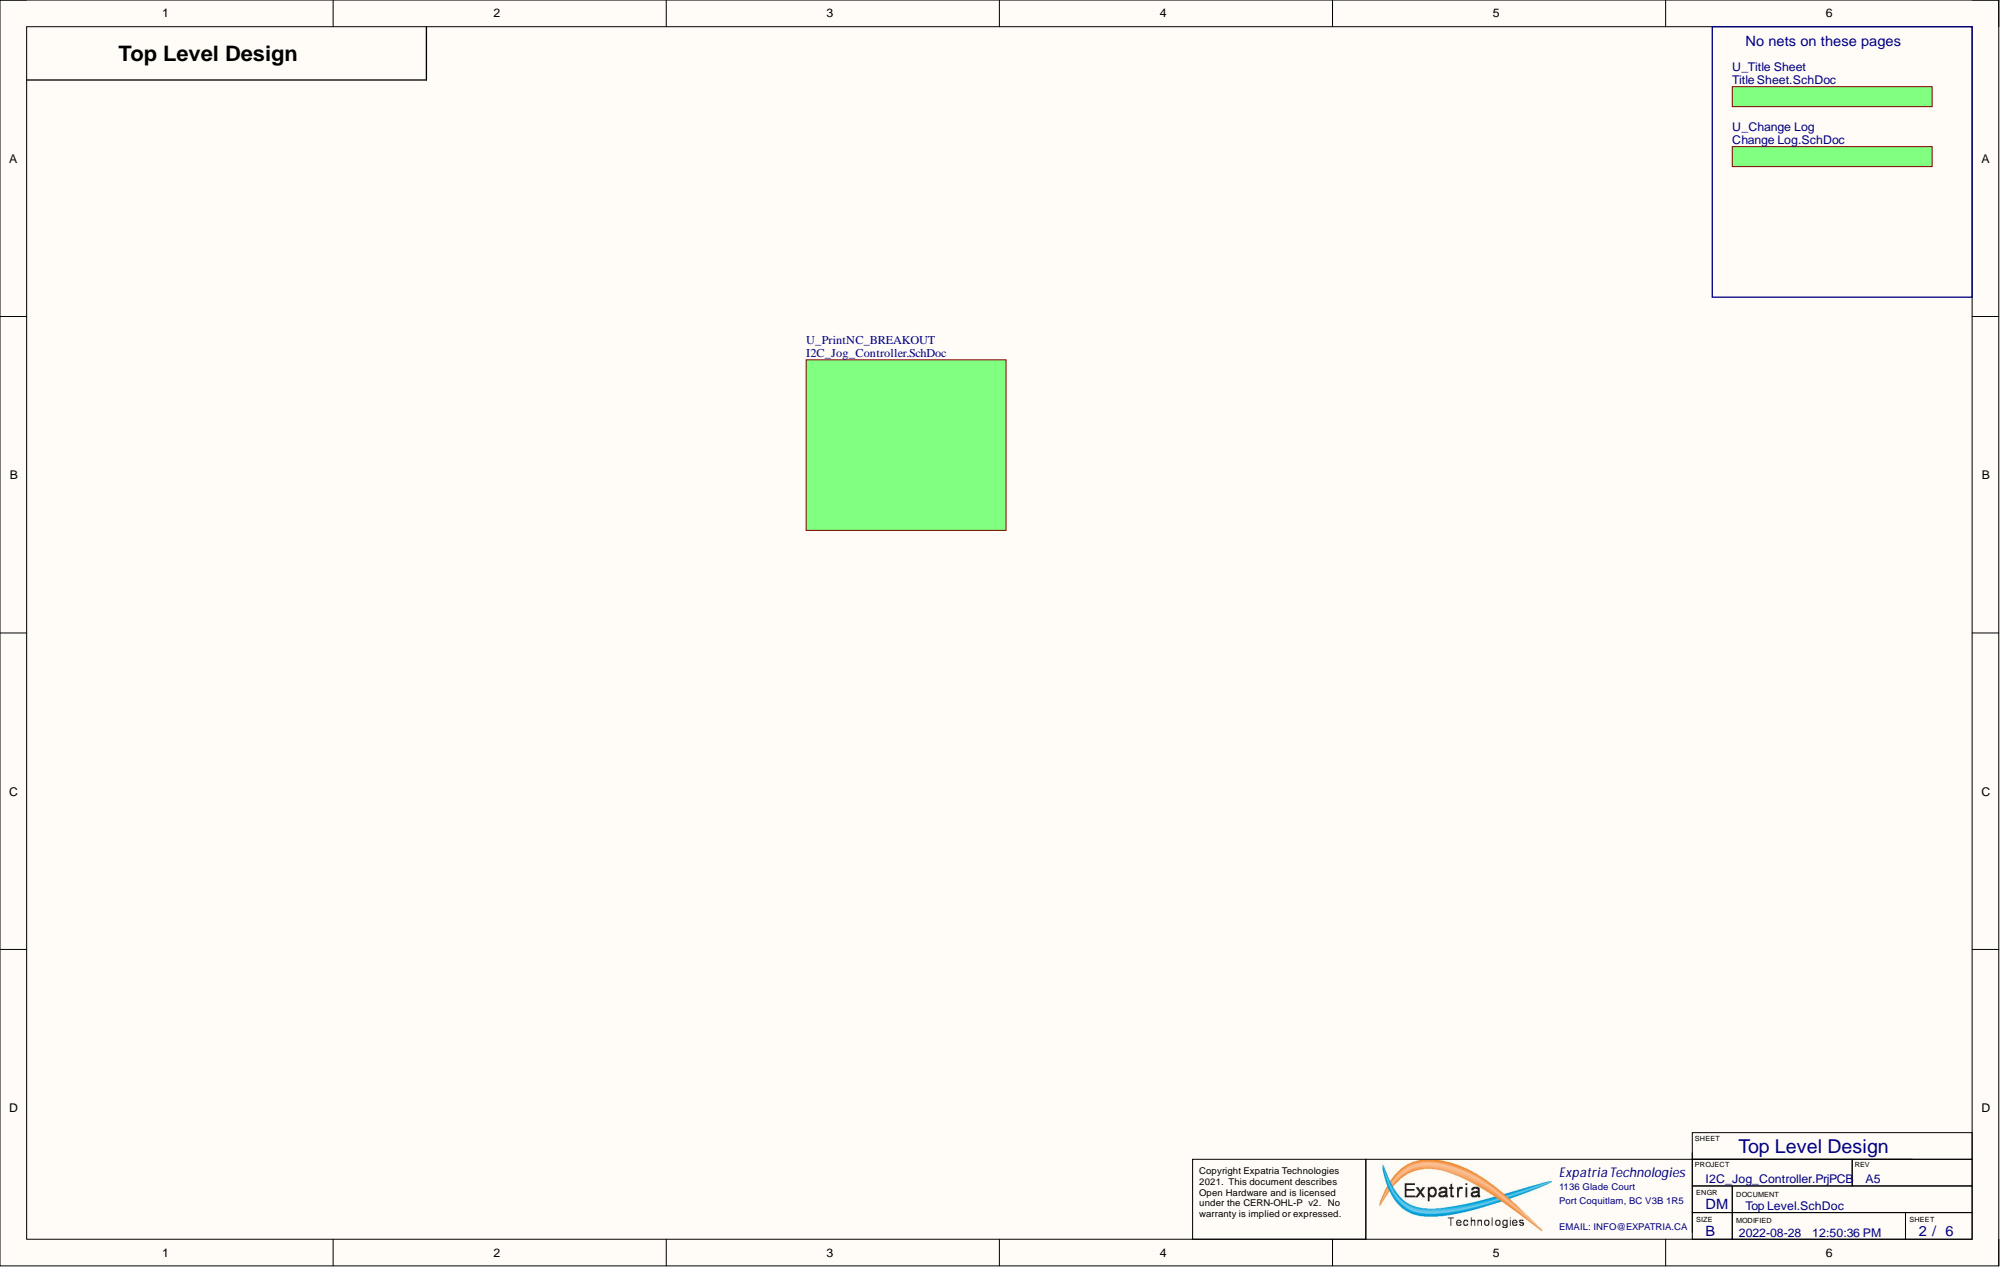
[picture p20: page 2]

No nets on these pages

Top Level.SchDoc

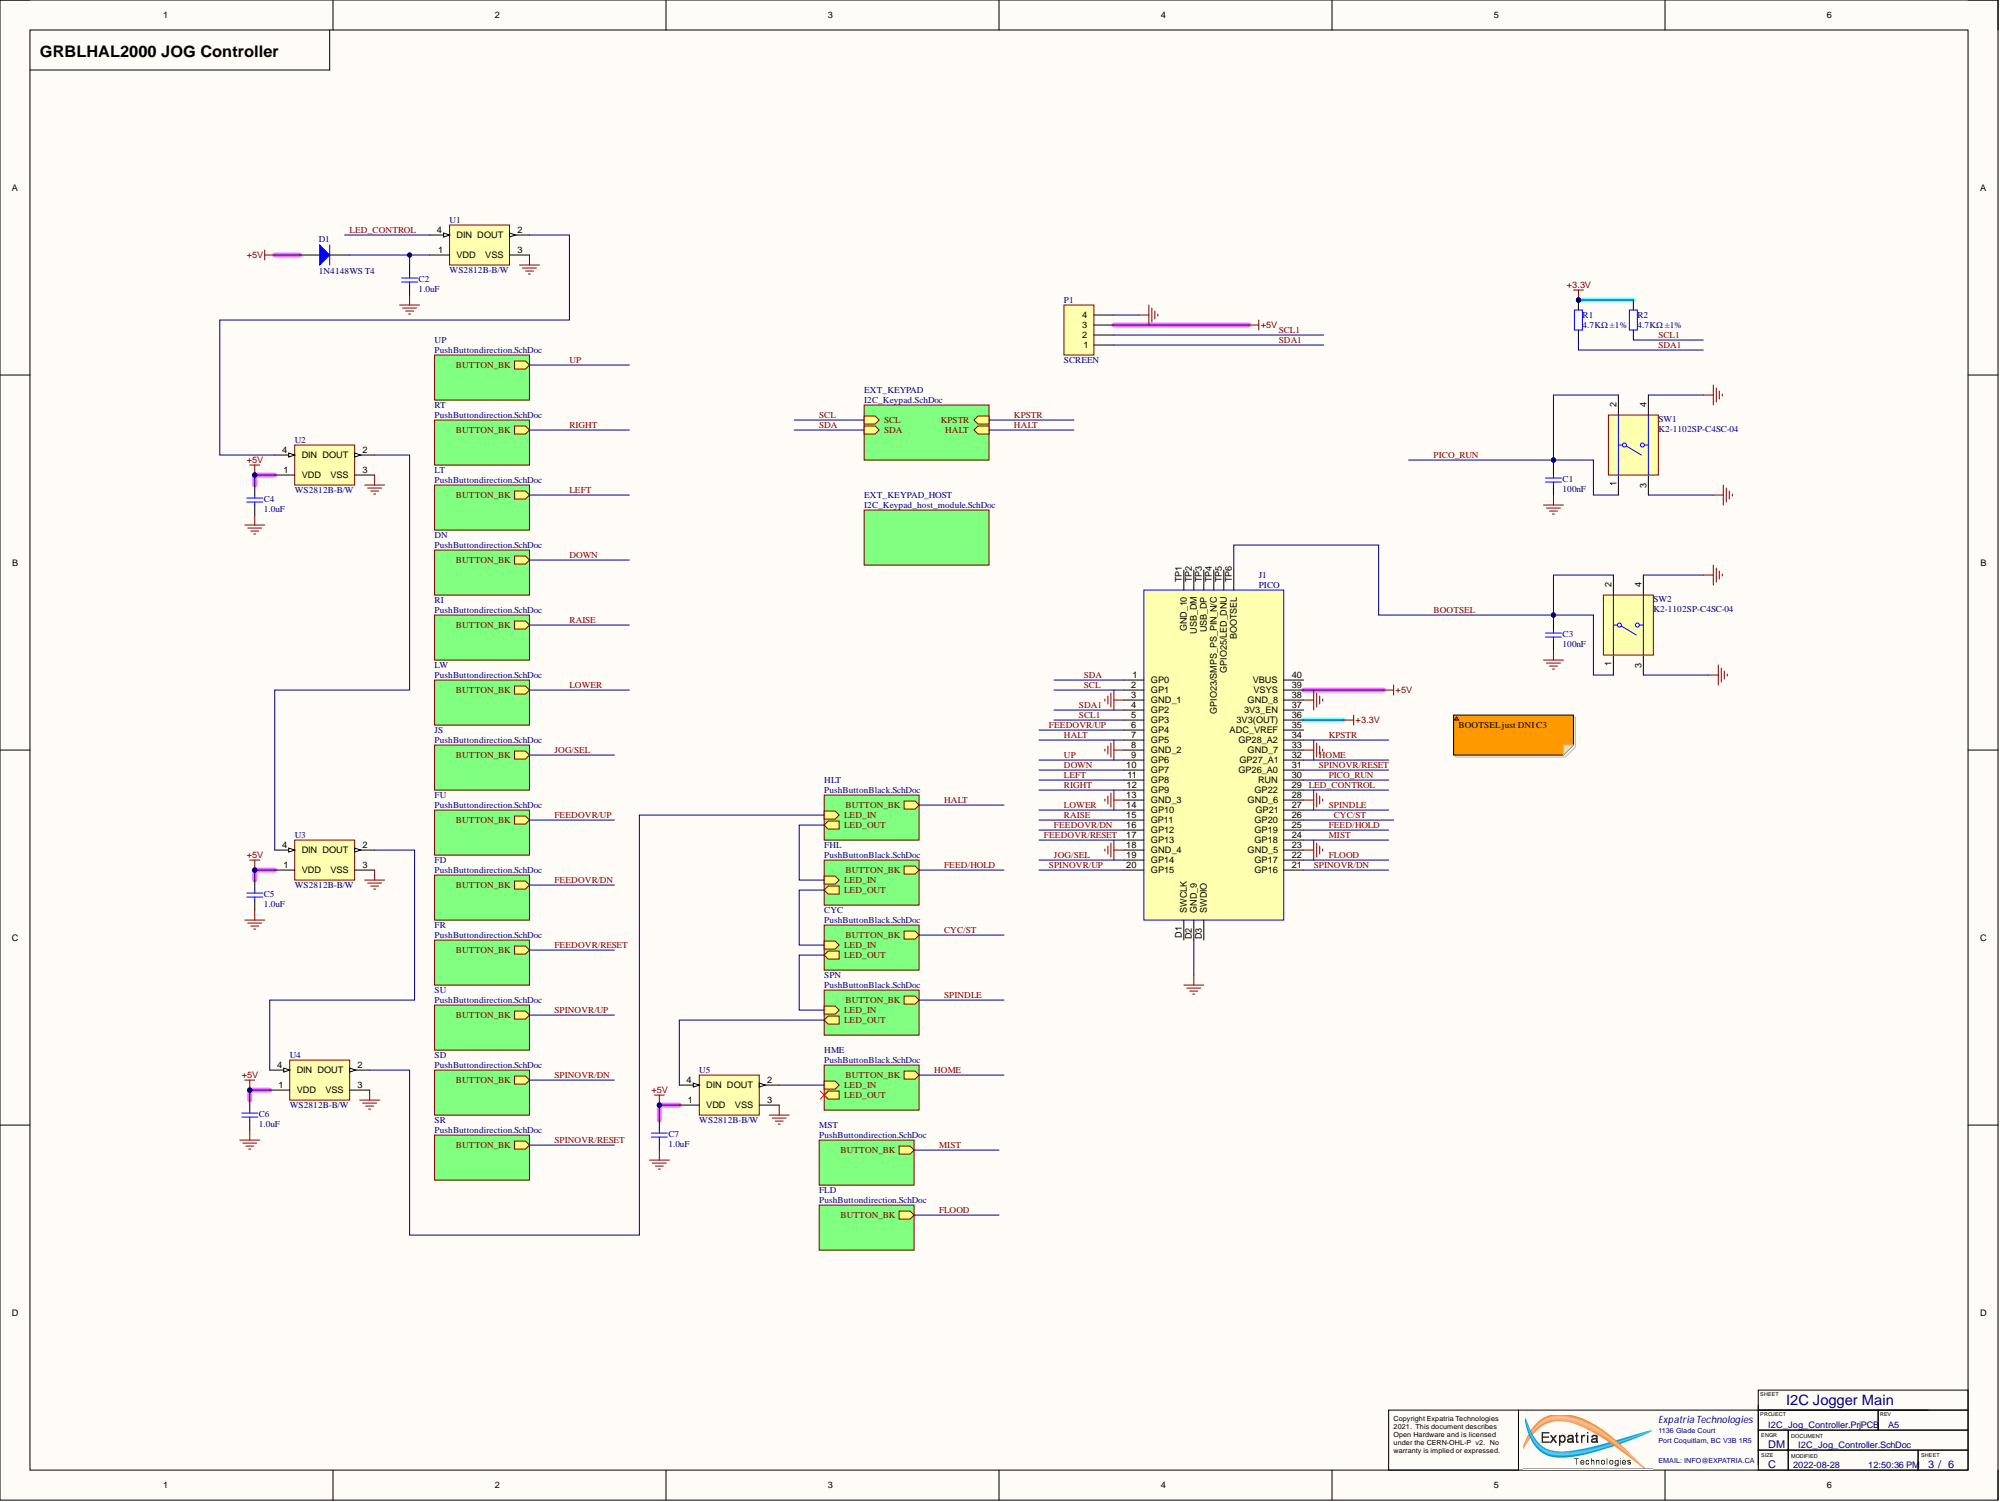
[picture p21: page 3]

warra nty i s i m p l i e d or e x pre s s e d . | | P R OJE C T I2C_Jog_Controller . P rj P C | R E V

B Copyright Expatria Technologies 2021. This document describes Open Hardware and is licensed under the CERN-OHL-P v2. No

E N G R | D O C U M E N T I2C_Jog_Controller S . c h D o c

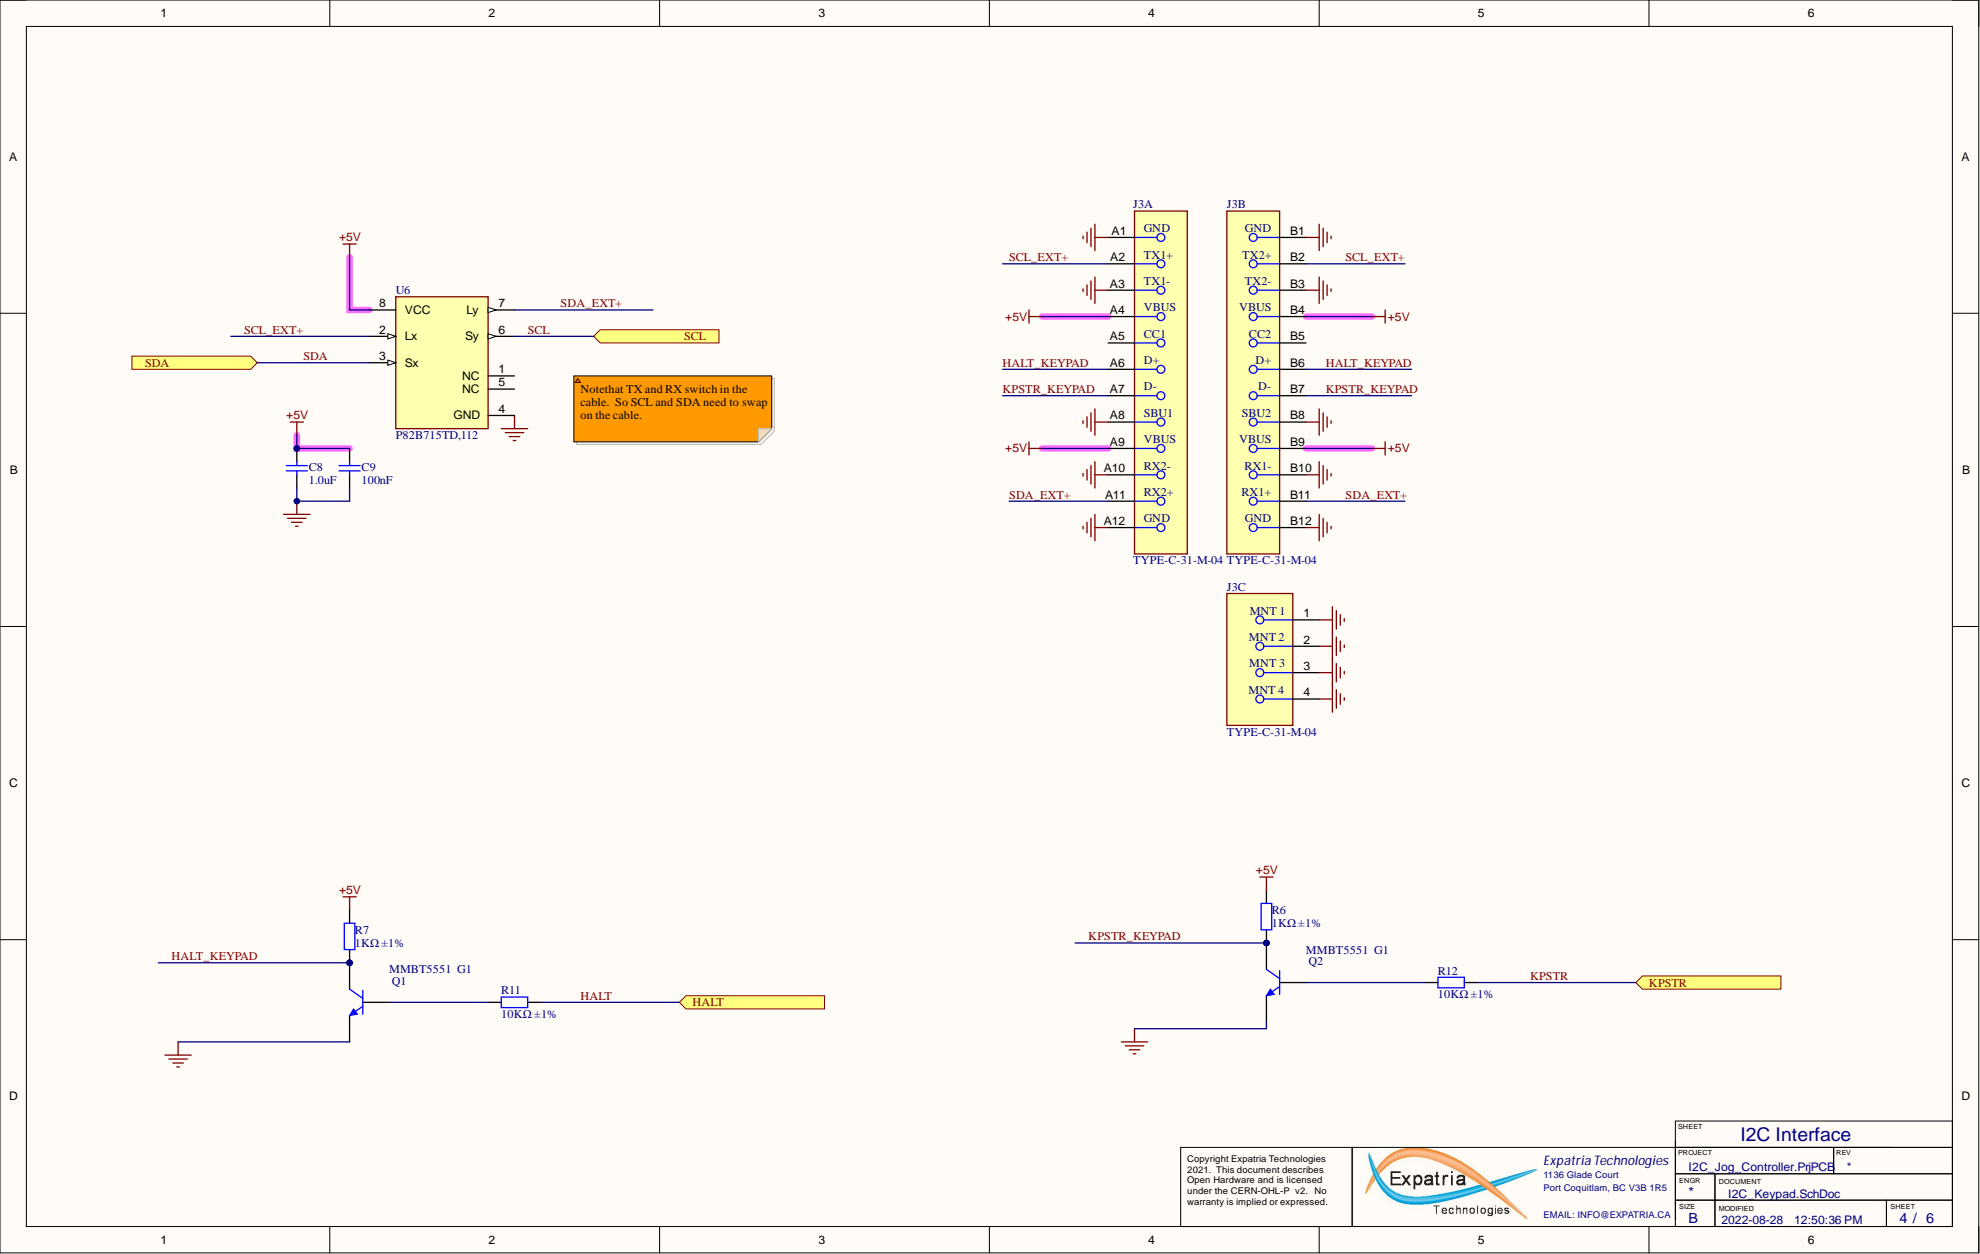
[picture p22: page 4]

cable. So SCL and SDA need to swap
on the cable.


TRIG 2

GND 1


Co p yri g ht Ex p atri a Te c h n o l o g i e s 1. Th i s d o c u m e nt d e s cri b e s O p e n Hardware a n d i s l i c e n s e d u n d er th e CERN-OHL-P v 2. No warra nty i s i m p l i e d or e x pre s s e d . | | P R OJE C T I2C_Jog_Controller . P rj P C | R E V

E N G R | D O C U M E N T PushBut tondirec tion. S c h D o c


This card is for use with A5 and A6
GRBLHAL2000.

HALT is already pulled up to 3.3V elsewhere.

AM | I2C_Keypad_host_module.SchDoc

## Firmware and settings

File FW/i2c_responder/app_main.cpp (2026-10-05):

/**
 * Example program for basic use of pico as an I2C peripheral (previously known as I2C slave)
 * 
 * This example allows the pico to act as a 256byte RAM
 * 
 * Author: Graham Smith (graham@smithg.co.uk)
 */


// Usage:
//
// When writing data to the pico the first data byte updates the current address to be used when writing or reading from the RAM
// Subsequent data bytes contain data that is written to the ram at the current address and following locations (current address auto increments)
//
// When reading data from the pico the first data byte returned will be from the ram storage located at current address
// Subsequent bytes will be returned from the following ram locations (again current address auto increments)
//
// N.B. if the current address reaches 255, it will autoincrement to 0 after next read / write

#include <stdio.h>
#include "pico/stdlib.h"
#include "hardware/i2c.h"
#include "hardware/irq.h"
#include "hardware/timer.h"
#include "hardware/gpio.h"
#include "hardware/flash.h"
#include "ss_oled.h"

#include "pico/stdio.h"
#include "pico/time.h"
#include <tusb.h>
#include "Adafruit_NeoPixel.hpp"

#include <i2c_fifo.h>
#include <i2c_slave.h>

#include <math.h>

#include "i2c_jogger.h"

//#define SHOWJOG 1
//#define SHOWOVER 1
#define SHOWRAM 1
#define TWOWAY 1

#define OLED_SCREEN_FLIP 1

#define TICK_TIMER_PERIOD 10
#define ROLLOVER_DELAY_PERIOD 7


uint8_t jog_color[] = {0,255,0};
uint8_t halt_color[] = {0,255,0};
uint8_t hold_color[] = {0,255,0};
uint8_t run_color[] = {0,255,0};
int32_t feed_color[] = {0,10000,0};
int32_t rpm_color[] = {0,10000,0};


Adafruit_NeoPixel pixels(NUMPIXELS, PIN, NEO_GRB + NEO_KHZ800);

// define I2C addresses to be used for this peripheral
static const uint I2C_SLAVE_ADDRESS = 0x49;
static const uint I2C_BAUDRATE = 100000; // 100 kHz

// GPIO pins to use for I2C SLAVE
static const uint I2C_SLAVE_SDA_PIN = 0;
static const uint I2C_SLAVE_SCL_PIN = 1;

// RPI Pico

int rc;
SSOLED oled;
static uint8_t ucBuffer[1024];
bool screenflip = false;
bool joggle_reset =false;

int led_update_counter = 0;
int update_neopixel_leds = 0;
int screen_update_counter = 0;
int status_update_counter = 0;
int onboard_led_count = 0;
int jogmode = 0;

int command_error = 0;

// ram_addr is the current address to be used when writing / reading the RAM
// N.B. the address auto increments, as stored in 8 bit value it automatically rolls round when reaches 255

static struct
{
    uint8_t mem[256];
    uint8_t version;
    uint8_t mem_address;
    bool mem_address_written;
} context;

char buf[8];

uint8_t ram_addr = 0;
uint8_t status_addr = 0;
uint8_t key_pressed = 0;
uint8_t key_character = '\0';

uint8_t feed_up_pressed = 0;
uint8_t feed_down_pressed = 0;
uint8_t feed_up_fine_pressed = 0;
uint8_t feed_down_fine_pressed = 0;
uint8_t feed_reset_pressed = 0;

uint8_t spin_up_pressed = 0;
uint8_t spin_down_pressed = 0;
uint8_t spin_up_fine_pressed = 0;
uint8_t spin_down_fine_pressed = 0;
uint8_t spin_reset_pressed = 0;

uint8_t jog_mod_pressed = 0;
uint8_t jog_mode_pressed = 0;
uint8_t jog_toggle_pressed = 0;

uint8_t mist_pressed = 0;
uint8_t flood_pressed = 0;
uint8_t spinoff_pressed = 0;
uint8_t home_pressed = 0;

uint8_t direction_pressed = 0;
uint8_t previous_direction_pressed = 0;
uint8_t keysent = 0;
int rollover_delay = 0;
int transition_delay = 0;

uint8_t macro_top_pressed = 0;
uint8_t macro_bot_pressed = 0;
uint8_t macro_left_pressed = 0;
uint8_t macro_right_pressed = 0;
uint8_t macro_lower_pressed = 0;
uint8_t macro_raise_pressed = 0;
uint8_t macro_home_pressed = 0;
uint8_t macro_spindle_pressed = 0;
uint8_t reset_pressed = 0;
uint8_t unlock_pressed = 0;
uint8_t halt_pressed = 0;

machine_status_packet_t *packet = (machine_status_packet_t*) context.mem;
machine_status_packet_t prev_packet;
machine_status_packet_t *previous_packet = &prev_packet;
//Jogmode previous_jogmode;
//Jogmodify previous_jogmodify;
ScreenMode previous_screenmode = DEFAULT;

char *ram_ptr = (char*) &context.mem[0];
int character_sent;

// Our handler is called from the I2C ISR, so it must complete quickly. Blocking calls /
// printing to stdio may interfere with interrupt handling.
static void i2c_slave_handler(i2c_inst_t *i2c, i2c_slave_event_t event) {
    switch (event) {
    case I2C_SLAVE_RECEIVE: // master has written some data
        if (!context.mem_address_written) {
            // writes always start with the memory address
            context.version = i2c_read_byte(i2c); // read struct version TODO: error checking on version
            context.mem_address = context.version == 0x02 ? 0x01 : context.version; // set address to 1
            context.mem_address_written = true;
        } else {
            // save into memory
            context.mem[context.mem_address] = i2c_read_byte(i2c);
            context.mem_address++;
        }
        break;
    case I2C_SLAVE_REQUEST: // master is requesting data
        // load from memory
        i2c_write_byte(i2c, context.mem[context.mem_address]);
        context.mem_address++;
        break;
    case I2C_SLAVE_FINISH: // master has signalled Stop / Restart
        context.mem_address_written = false;
        break;
    default:
        break;
    }
}

static void setup_slave() {
    gpio_init(I2C_SLAVE_SDA_PIN);
    gpio_set_function(I2C_SLAVE_SDA_PIN, GPIO_FUNC_I2C);
    gpio_pull_up(I2C_SLAVE_SDA_PIN);

    gpio_init(I2C_SLAVE_SCL_PIN);
    gpio_set_function(I2C_SLAVE_SCL_PIN, GPIO_FUNC_I2C);
    gpio_pull_up(I2C_SLAVE_SCL_PIN);

    i2c_init(i2c0, I2C_BAUDRATE);
    // configure I2C0 for slave mode
    i2c_slave_init(i2c0, I2C_SLAVE_ADDRESS, &i2c_slave_handler);
}

uint8_t adjust (uint8_t value) {
	if (NEO_BRIGHTNESS == 0) return value ;
	return ((value * neopixels_gamma8(NEO_BRIGHTNESS)) >> 8) ;
};

volatile bool timer_fired = false;

uint8_t keypad_sendchar (uint8_t character, bool clearpin, bool update_status) {
  //maybe use key_pressed variable to avoid spamming?
  int timeout = I2C_TIMEOUT_VALUE;

  command_error = 0;

  gpio_put(ONBOARD_LED, 0);

  while (context.mem_address_written != false && context.mem_address>0);

  context.mem[0] = character;
  context.mem_address = 0;
  //gpio_put(KPSTR_PIN, false);
  sleep_us(1000);
  gpio_put(KPSTR_PIN, true);
  //sleep_us(100);
  while (context.mem_address == 0 && timeout){
    sleep_us(1);      
    timeout = timeout - 1;}

  if(!timeout)
    command_error = 1;
  //sleep_ms(2);
  if (clearpin){
    //sleep_ms(5);
    gpio_put(KPSTR_PIN, false);
  }
  gpio_put(ONBOARD_LED, 1);
  return true;
};

static void update_neopixels(void){

  if (context.mem_address_written || (packet->status_code == Status_UserException))// < offsetof(machine_status_packet_t, msgtype))
    return;
  
  //set override LEDS
  if (packet->feed_override > 100)
    feed_color[0] = ((packet->feed_override - 100) * 255)/100;
  else
    feed_color[0] = 0;
  if (packet->feed_override > 100)
    feed_color[1] = 255 - (((packet->feed_override - 100) * 255)/100);
  else
    feed_color[1] = 255- (((100-packet->feed_override) * 255)/100);
  if(packet->feed_override < 100)
    feed_color[2] = ((100 - packet->feed_override) * 255)/100;
  else
    feed_color[2] = 0;

  if (packet->spindle_override > 100)
    rpm_color[0] = ((packet->spindle_override - 100) * 255)/100;
  else
    rpm_color[0] = 0;
  if (packet->spindle_override > 100)
    rpm_color[1] = 255 - (((packet->spindle_override - 100) * 255)/100);
  else
    rpm_color[1] = 255- (((100-packet->spindle_override) * 255)/100);
  if(packet->spindle_override < 100)
    rpm_color[2] = ((100 - packet->spindle_override) * 255)/100;
  else
    rpm_color[2] = 0;    

  pixels.setPixelColor(FEEDLED,pixels.Color((uint8_t) feed_color[0], (uint8_t) feed_color[1], (uint8_t) feed_color[2]));
  pixels.setPixelColor(SPINLED,pixels.Color(rpm_color[0], rpm_color[1], rpm_color[2]));

  //set home LED
  if(packet->machine_modes.homed)
    pixels.setPixelColor(HOMELED,pixels.Color(0, 255, 0));
  else
    pixels.setPixelColor(HOMELED,pixels.Color(200, 135, 0));

  //set spindleoff LED
  if(packet->spindle_rpm > 0)
    pixels.setPixelColor(SPINDLELED,pixels.Color(255, 75, 0));
  else
    pixels.setPixelColor(SPINDLELED,pixels.Color(75, 255, 130));

  //set Coolant LED
  if(packet->coolant_state.value)
    pixels.setPixelColor(COOLED,pixels.Color(0, 100, 255));
  else
    pixels.setPixelColor(COOLED,pixels.Color(0, 0, 100));  

  //preload jog LED colors depending on speed
  switch (packet->jog_mode.mode) {
  case FAST :
    jog_color[0] = 255; jog_color[1] = 0; jog_color[2] = 0; //RGB
    break;
  case SLOW : 
    jog_color[0] = 0; jog_color[1] = 255; jog_color[2] = 0; //RGB      
    break;
  case STEP : 
    jog_color[0] = 0; jog_color[1] = 0; jog_color[2] = 255; //RGB      
    break;
  default :
    //jog_color[0] = 255; jog_color[1] = 255; jog_color[2] = 255; //RGB
  break;      
  }//close jogmode

  switch (packet->system_state){
    case SystemState_Idle :
    //no change to jog colors
      run_color[0] = 0; run_color[1] = 255; run_color[2] = 0; //RGB
      hold_color[0] = 255; hold_color[1] = 150; hold_color[2] = 0; //RGB
      halt_color[0] = 255; halt_color[1] = 0; halt_color[2] = 0; //RGB   
    break; //close idle case

    case SystemState_Hold :
    //no jog during hold to jog colors
      run_color[0] = 0; run_color[1] = 255; run_color[2] = 0; //RGB
      hold_color[0] = 255; hold_color[1] = 150; hold_color[2] = 0; //RGB
      halt_color[0] = 255; halt_color[1] = 0; halt_color[2] = 0; //RGB
      jog_color[0] = 0; jog_color[1] = 0; jog_color[2] = 0; //RGB     
    break; //close idle case

    case SystemState_ToolChange : 
    //no change to jog colors
      run_color[0] = 0; run_color[1] = 255; run_color[2] = 0; //RGB
      hold_color[0] = 255; hold_color[1] = 150; hold_color[2] = 0; //RGB
      halt_color[0] = 255; halt_color[1] = 0; halt_color[2] = 0; //RGB   
    break;//close tool change case 

    case SystemState_Jog :
        //Indicate jog in progress
      run_color[0] = 0; run_color[1] = 255; run_color[2] = 0; //RGB
      hold_color[0] = 255; hold_color[1] = 150; hold_color[2] = 0; //RGB
      halt_color[0] = 255; halt_color[1] = 0; halt_color[2] = 0; //RGB        
      jog_color[0] = 255; jog_color[1] = 150; jog_color[2] = 0; //RGB
    break;//close jog case

    case SystemState_Homing :
        //No jogging during homing
      run_color[0] = 0; run_color[1] = 255; run_color[2] = 0; //RGB
      hold_color[0] = 255; hold_color[1] = 150; hold_color[2] = 0; //RGB
      halt_color[0] = 255; halt_color[1] = 0; halt_color[2] = 0; //RGB        
      jog_color[0] = 0; jog_color[1] = 0; jog_color[2] = 0; //RGB    
    break;//close homing case

    case SystemState_Cycle :
      //No jogging during job
      run_color[0] = 0; run_color[1] = 255; run_color[2] = 0; //RGB
      hold_color[0] = 255; hold_color[1] = 150; hold_color[2] = 0; //RGB
      halt_color[0] = 255; halt_color[1] = 0; halt_color[2] = 0; //RGB        
      jog_color[0] = 0; jog_color[1] = 0; jog_color[2] = 0; //RGB     
    break;//close cycle state

    case SystemState_Alarm :
          //handle alarm state at bottom
      jog_color[0] = 0; jog_color[1] = 0; jog_color[2] = 0; //RGB
      //run_color[0] = 255; run_color[1] = 0; run_color[2] = 0; //RGB
      //hold_color[0] = 255; hold_color[1] = 0; hold_color[2] = 0; //RGB   
      halt_color[0] = 255; halt_color[1] = 0; halt_color[2] = 0; //RGB 

      //also override above colors for maximum alarm 
      pixels.setPixelColor(SPINDLELED,pixels.Color(255, 0, 0));
      pixels.setPixelColor(COOLED,pixels.Color(255, 0, 0));
      pixels.setPixelColor(HOMELED,pixels.Color(255, 0, 0));
      pixels.setPixelColor(SPINLED,pixels.Color(255, 0, 0));
      pixels.setPixelColor(FEEDLED,pixels.Color(255, 0, 0));
    break;//close alarm state

    default :  //this is active when there is a non-interactive controller
      //run_color[0] = 0; run_color[1] = 255; run_color[2] = 0; //RGB
      //hold_color[0] = 255; hold_color[1] = 150; hold_color[2] = 0; //RGB
      //halt_color[0] = 255; halt_color[1] = 0; halt_color[2] = 0; //RGB   

    break;//close alarm state
  }//close system_state switch statement

  if(screenmode == JOG_MODIFY){
    //some overrides for alternate functions
    //violet = (138, 43, 226)
    //jog_color[0] = 138; jog_color[1] = 43; jog_color[2] = 226;
    //run_color[0] = 138; run_color[1] = 43; run_color[2] = 226; //RGB
    //hold_color[0] = 138; hold_color[1] = 43; hold_color[2] = 226; //RGB   
    //halt_color[0] = 0; halt_color[1] = 0; halt_color[2] = 0; //RGB 
    pixels.setPixelColor(COOLED,pixels.Color(138, 43, 226));
    pixels.setPixelColor(HOMELED,pixels.Color(138, 43, 226));
    //pixels.setPixelColor(FEEDLED,pixels.Color(0, 0, 0));
    //pixels.setPixelColor(SPINLED,pixels.Color(0, 0, 0));
  }

  //set jog LED values
  if(screenmode == JOG_MODIFY)
    pixels.setPixelColor(JOGLED,pixels.Color(138, 43, 226));
  else
    pixels.setPixelColor(JOGLED,pixels.Color(jog_color[0], jog_color[1], jog_color[2]));

  if(isnan(packet->coordinate.a) && screenmode == JOG_MODIFY)
    pixels.setPixelColor(RAISELED,pixels.Color(138, 43, 226));
  else
    pixels.setPixelColor(RAISELED,pixels.Color(jog_color[0], jog_color[1], jog_color[2]));
  pixels.setPixelColor(HALTLED,pixels.Color(halt_color[0], halt_color[1], halt_color[2]));
  pixels.setPixelColor(HOLDLED,pixels.Color(hold_color[0], hold_color[1], hold_color[2]));
  pixels.setPixelColor(RUNLED,pixels.Color(run_color[0], run_color[1], run_color[2]));

  pixels.show();
}

void activate_jogled(void){
  jog_color[0] = 255; jog_color[1] = 150; jog_color[2] = 0; //RGB
  pixels.setPixelColor(JOGLED,pixels.Color(jog_color[0], jog_color[1], jog_color[2]));
  pixels.setPixelColor(RAISELED,pixels.Color(jog_color[0], jog_color[1], jog_color[2]));
  pixels.show();
}

// Converts an uint32 variable to string.
char *uitoa (uint32_t n)
{
    char *bptr = buf + sizeof(buf);

    *--bptr = '\0';

    if (n == 0)
        *--bptr = '0';
    else while (n) {
        *--bptr = '0' + (n % 10);
        n /= 10;
    }

    return bptr;
}

static char *map_coord_system (coord_system_id_t id)
{
    uint8_t g5x = id + 54;

    strcpy(buf, uitoa((uint32_t)(g5x > 59 ? 59 : g5x)));
    if(g5x > 59) {
        strcat(buf, ".");
        strcat(buf, uitoa((uint32_t)(g5x - 59)));
    }

    return buf;
}
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
int main() {

  stdio_init_all();

  gpio_init(KPSTR_PIN);
  gpio_set_dir(KPSTR_PIN, GPIO_OUT);

  gpio_init(HALTBUTTON);
  gpio_set_dir(HALTBUTTON, GPIO_IN);
  gpio_set_pulls(HALTBUTTON,true,false);

  gpio_init(UPBUTTON);
  gpio_set_dir(UPBUTTON, GPIO_IN);
  gpio_set_pulls(UPBUTTON,true,false);

  gpio_init(DOWNBUTTON);
  gpio_set_dir(DOWNBUTTON, GPIO_IN);
  gpio_set_pulls(DOWNBUTTON,true,false);

  gpio_init(LEFTBUTTON);
  gpio_set_dir(LEFTBUTTON, GPIO_IN);
  gpio_set_pulls(LEFTBUTTON,true,false);

  gpio_init(RIGHTBUTTON);
  gpio_set_dir(RIGHTBUTTON, GPIO_IN);
  gpio_set_pulls(RIGHTBUTTON,true,false);

  gpio_init(LOWERBUTTON);
  gpio_set_dir(LOWERBUTTON, GPIO_IN);
  gpio_set_pulls(LOWERBUTTON,true,false);

  gpio_init(RAISEBUTTON);
  gpio_set_dir(RAISEBUTTON, GPIO_IN);
  gpio_set_pulls(RAISEBUTTON,true,false);

  gpio_init(JOG_SELECT);
  gpio_set_dir(JOG_SELECT, GPIO_IN);
  gpio_set_pulls(JOG_SELECT,true,false);

  gpio_init(FEEDOVER_UP);
  gpio_set_dir(FEEDOVER_UP, GPIO_IN);
  gpio_set_pulls(FEEDOVER_UP,true,false);
  
  gpio_init(FEEDOVER_DOWN);
  gpio_set_dir(FEEDOVER_DOWN, GPIO_IN);
  gpio_set_pulls(FEEDOVER_DOWN,true,false);

  gpio_init(FEEDOVER_RESET);
  gpio_set_dir(FEEDOVER_RESET, GPIO_IN);
  gpio_set_pulls(FEEDOVER_RESET,true,false);

  gpio_init(SPINDLEBUTTON);
  gpio_set_dir(SPINDLEBUTTON, GPIO_IN);
  gpio_set_pulls(SPINDLEBUTTON,true,false);

  gpio_init(RUNBUTTON);
  gpio_set_dir(RUNBUTTON, GPIO_IN);
  gpio_set_pulls(RUNBUTTON,true,false);

  gpio_init(HOLDBUTTON);
  gpio_set_dir(HOLDBUTTON, GPIO_IN);
  gpio_set_pulls(HOLDBUTTON,true,false);

  gpio_init(MISTBUTTON);
  gpio_set_dir(MISTBUTTON, GPIO_IN);
  gpio_set_pulls(MISTBUTTON,true,false);

  gpio_init(FLOODBUTTON);
  gpio_set_dir(FLOODBUTTON, GPIO_IN);
  gpio_set_pulls(FLOODBUTTON,true,false);

  gpio_init(HOMEBUTTON);
  gpio_set_dir(HOMEBUTTON, GPIO_IN);
  gpio_set_pulls(HOMEBUTTON,true,false);

  gpio_init(SPINOVER_UP);
  gpio_set_dir(SPINOVER_UP, GPIO_IN);
  gpio_set_pulls(SPINOVER_UP,true,false);

  gpio_init(SPINOVER_DOWN);
  gpio_set_dir(SPINOVER_DOWN, GPIO_IN);
  gpio_set_pulls(SPINOVER_DOWN,true,false);

  gpio_init(SPINOVER_RESET);
  gpio_set_dir(SPINOVER_RESET, GPIO_IN);
  gpio_set_pulls(SPINOVER_RESET,true,false);

  gpio_init(ONBOARD_LED);
  gpio_set_dir(ONBOARD_LED, GPIO_OUT);
  gpio_put(ONBOARD_LED, 1);
  sleep_ms(250);
  gpio_put(ONBOARD_LED, 0);
  sleep_ms(250);
  gpio_put(ONBOARD_LED, 1);

  struct repeating_timer timer;
  add_repeating_timer_ms(TICK_TIMER_PERIOD, tick_timer_callback, NULL, &timer);
  
  pixels.begin(); // INITIALIZE NeoPixel strip object (REQUIRED)
  pixels.setBrightnessFunctions(adjust,adjust,adjust,adjust);
  
  pixels.clear(); // Set all pixel colors to 'off'
  pixels.setPixelColor(JOGLED,pixels.Color(255, 255, 255));
  pixels.setPixelColor(RAISELED,pixels.Color(255, 255, 255)); 
  pixels.setPixelColor(HALTLED,pixels.Color(255, 255, 255));
  pixels.setPixelColor(FEEDLED,pixels.Color(255, 255, 255));
  pixels.setPixelColor(SPINLED,pixels.Color(255, 255, 255));
  pixels.setPixelColor(COOLED,pixels.Color(255, 255, 255));
  pixels.setPixelColor(HOLDLED,pixels.Color(255, 255, 255));
  pixels.setPixelColor(RUNLED,pixels.Color(255, 255, 255));
  pixels.setPixelColor(SPINDLELED,pixels.Color(255, 255, 255));
  pixels.setPixelColor(HOMELED,pixels.Color(255, 255, 255));
  pixels.show();   // Send the updated pixel colors to the hardware.


// Setup I2C0 as slave (peripheral)
setup_slave();
packet->system_state = SystemState_Undefined; // ADD STATUS FOR CONTROLLER DISCONNECTED?
packet->status_code = Status_UserException; // ADD STATUS FOR CONTROLLER DISCONNECTED?
key_character = CMD_STATUS_REPORT_LEGACY;
//keypad_sendchar (key_character, 1, 1);
status_update_counter = STATUS_REQUEST_PERIOD;

if (*flash_target_contents != 0xff)
  screenflip = *flash_target_contents;

uint8_t uc[8];
int i, j;
char szTemp[32];
    
rc = oledInit(&oled, OLED_128x64, 0x3c, screenflip, 0, 0, SDA_PIN, SCL_PIN, RESET_PIN, 1000000L);
oledSetBackBuffer(&oled, ucBuffer);
oledFill(&oled, 0,1);
oledWriteString(&oled, 0,0,1,(char *)"JOG2K", FONT_12x16, 0, 1);
oledWriteString(&oled, 0,0,4,(char *)JOG2K_VERSION, FONT_8x8, 0, 1);
oledWriteString(&oled, 0,0,7,(char *)PLUGIN_VERSION, FONT_6x8, 0, 1);
sleep_ms(1000);
oledFill(&oled, 0,1);

draw_main_screen(1);

    // Main loop handles the buttons, everything else handled in interrupts
    while (true) {

        //draw_main_screen(1);
        
        // if (!packet->machine_state.disconnected){
        //   current_jogmode = (Jogmode) (packet->jog_mode.mode);
        //   current_jogmodify =  (Jogmodify) (packet->jog_mode.modifier);
        // }

        if( packet->system_state != previous_packet->system_state ||
            packet->feed_override != previous_packet->feed_override ||
            packet->spindle_override != previous_packet->spindle_override||
            packet->jog_mode.value != previous_packet->jog_mode.value ||
            packet->coordinate.x != previous_packet->coordinate.x ||
            packet->coordinate.y != previous_packet->coordinate.y ||
            packet->coordinate.z != previous_packet->coordinate.z ||
            (!isnan(packet->coordinate.a) && (packet->coordinate.a != previous_packet->coordinate.a)) ||                  
            packet->current_wcs != previous_packet->current_wcs ||
            packet->jog_stepsize != previous_packet->jog_stepsize ||
            packet->feed_rate != previous_packet->feed_rate ||
            packet->spindle_rpm != previous_packet->spindle_rpm ||
            packet->jog_mode.modifier != previous_packet->jog_mode.modifier ||
            screenmode != previous_screenmode
            ){          
          draw_main_screen(1);        
        }

        //if(screenmode != previous_screenmode)
        //  draw_main_screen(1);
        
        if(packet->system_state == SystemState_Jog){
          draw_main_screen(1);
          update_neopixels();
        }

        if (update_neopixel_leds && (packet->status_code != Status_UserException) ){
          if(!context.mem_address_written) // >= offsetof(machine_status_packet_t, msgtype))          
            update_neopixels();
          update_neopixel_leds = 0;
        }
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

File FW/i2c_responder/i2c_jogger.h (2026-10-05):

#ifndef __I2C_JOGGER_H__
#define __I2C_JOGGER_H__

#define PLUGIN_VERSION "PLUGIN: Keypad v1.47"
#define JOG2K_FW_VERSION "1.2.1"

#ifndef BUILD_SHA
#define BUILD_SHA "eng"
#endif

#define JOG2K_VERSION "v" JOG2K_FW_VERSION "+" BUILD_SHA

// Which pin on the Arduino is connected to the NeoPixels?
#define PIN        22 // On Trinket or Gemma, suggest changing this to 1
// How many NeoPixels are attached to the Arduino?
#define NUMPIXELS 10 // Popular NeoPixel ring size
#define DELAYVAL 200 // Time (in milliseconds) to pause between pixels
#define CYCLEDELAY 12 // Time to wait after a cycle
#define NEO_BRIGHTNESS 128

//flash defines
#define FLASH_TARGET_OFFSET (256 * 1024)
const uint8_t *flash_target_contents = (const uint8_t *) (XIP_BASE + FLASH_TARGET_OFFSET);

#define SDA_PIN 2
#define SCL_PIN 3
#define RESET_PIN -1

// #define STATE_ALARM         1 //!< In alarm state. Locks out all g-code processes. Allows settings access.
// #define STATE_CYCLE         2 //!< Cycle is running or motions are being executed.
// #define STATE_HOLD          3 //!< Active feed hold
// #define STATE_TOOL_CHANGE   4 //!< Manual tool change, similar to #STATE_HOLD - but stops spindle and allows jogging.
// #define STATE_IDLE          5 //!< Must be zero. No flags.
// #define STATE_HOMING        6 //!< Performing homing cycle
// #define STATE_JOG           7 //!< Jogging mode.
// #define STATE_RESET         8 //!< Screen set when reset is issued.
                 
// #define NORMAL_MODE         0
// #define LASER_MODE          1
// #define LATHE_MODE          2

//#define STATE_DISCONNECTED  1

// typedef union {
//     uint8_t value;                 //!< Bitmask value
//     struct {
//         uint8_t 
//         state        :4, //Machine state machine status
//         mode         :3, //machine mode
//         disconnected :1; //Connection status 
//     };
// } machine_state_t;

#define OLED_WIDTH 128
#define OLED_HEIGHT 64

//neopixel led locations
#define RAISELED 0
#define JOGLED 1
#define SPINLED 2
#define FEEDLED 3
#define HALTLED 4
#define HOLDLED 5
#define RUNLED 6
#define SPINDLELED 7
#define COOLED 8
#define HOMELED 9

#define KPSTR_PIN 28

#define HALTBUTTON 5
#define RUNBUTTON 20
#define HOLDBUTTON 19

#define JOG_SELECT 14
#define UPBUTTON 6
#define DOWNBUTTON 7
#define LEFTBUTTON 8
#define RIGHTBUTTON 9
#define LOWERBUTTON 10
#define RAISEBUTTON 11

#define FEEDOVER_UP 4
#define FEEDOVER_DOWN 12
#define FEEDOVER_RESET 13

#define SPINOVER_UP 15
#define SPINOVER_DOWN 16
#define SPINOVER_RESET 26

#define SPINDLEBUTTON 21
#define FLOODBUTTON 17
#define MISTBUTTON 18
#define HOMEBUTTON 27

#define ONBOARD_LED 25

#define LED_UPDATE_PERIOD 10
#define KEYPAD_UPDATE_PERIOD 10
#define SCREEN_UPDATE_PERIOD 20
#define STATUS_REQUEST_PERIOD 100

//ACTION DEFINES
#define MACROUP         0xB0 //MACRO_KEY0
#define MACRODOWN       0xB1 //MACRO_KEY1
#define MACROLEFT       0xB2 //MACRO_KEY2
#define MACRORIGHT      0xB3 //MACRO_KEY3
#define MACROSPINDLE    0xB4 //MACRO_KEY4
#define MACRORAISE      0xB5 //MACRO_KEY5
#define MACROLOWER      0xB6 //MACRO_KEY6

#define LASERSHUTTER    0xBA //LASER_SHUTTER
#define LASERPILOT      0xBB //LASER_PILOT

#define POWDER1SELECT   0xB6 //MACRO_KEY6 (REMAP to POWDER1 +FUNCTION)
#define POWDER2SELECT   0xB7 //MACRO_KEY7 (REMAP to POWDER2 +FUNCTION)

#define MACROHOME   'o'  //toggle WCS offset
#define RESET  0x18
#define UNLOCK 'X'

#define UP 0
#define RIGHT 1
#define DOWN 2
#define LEFT 3
#define RAISE 4
#define LOWER 5

//keycode mappings:
#define JOG_XR   0b00000010
#define JOG_XL   0b00001000
#define JOG_YF   0b00000100
#define JOG_YB   0b00000001
#define JOG_ZU   0b00010000
#define JOG_ZD   0b00100000
#define JOG_XRYF JOG_XR | JOG_YB
#define JOG_XRYB JOG_XR | JOG_YF
#define JOG_XLYF JOG_XL | JOG_YB
#define JOG_XLYB JOG_XL | JOG_YF
#define JOG_AR   0b10000000
#define JOG_AL   0b01000000
/*#define JOG_XRZU JOG_XR | JOG_ZU
#define JOG_XRZD JOG_XR | JOG_ZD
#define JOG_XLZU JOG_XL | JOG_ZU
#define JOG_XLZD JOG_XL | JOG_ZD*/

#define CHAR_XR   'R'
#define CHAR_XL   'L'
#define CHAR_YF   'F'
#define CHAR_YB   'B'
#define CHAR_ZU   'U'
#define CHAR_ZD   'D'
#define CHAR_XRYF 'r'
#define CHAR_XRYB 'q'
#define CHAR_XLYF 's'
#define CHAR_XLYB 't'
#define CHAR_XRZU 'w'
#define CHAR_XRZD 'v'
#define CHAR_XLZU 'u'
#define CHAR_XLZD 'x'
#define CHAR_AR   'A'
#define CHAR_AL   'a'

#define CMD_STATUS_REPORT_LEGACY '?'
#define CMD_CYCLE_START 0x81   // TODO: use 0x06 ctrl-F ACK instead? or SYN/DC2/DC3?
#define CMD_FEED_HOLD 0x82     // TODO: use 0x15 ctrl-U NAK instead?
#define CMD_RESET 0x18 // ctrl-X (CAN)
#define CMD_SAFETY_DOOR 0x84
#define CMD_OVERRIDE_FAN0_TOGGLE 0x8A       // Toggle Fan 0 on/off, not implemented by the core.
#define CMD_MPG_MODE_TOGGLE 0x8B            // Toggle MPG mode on/off, not implemented by the core.
#define CMD_AUTO_REPORTING_TOGGLE 0x8C      // Toggle auto real time reporting if configured.
#define CMD_OVERRIDE_FEED_RESET 0x90        // Restores feed override value to 100%.
#define CMD_OVERRIDE_FEED_COARSE_PLUS 0x91
#define CMD_OVERRIDE_FEED_COARSE_MINUS 0x92
#define CMD_OVERRIDE_FEED_FINE_PLUS 0x93
#define CMD_OVERRIDE_FEED_FINE_MINUS 0x94
#define CMD_OVERRIDE_RAPID_RESET 0x95       // Restores rapid override value to 100%.
#define CMD_OVERRIDE_RAPID_MEDIUM 0x96
#define CMD_OVERRIDE_RAPID_LOW 0x97
#define CMD_OVERRIDE_SPINDLE_RESET 0x99     // Restores spindle override value to 100%.
#define CMD_OVERRIDE_SPINDLE_COARSE_PLUS 0x9A
#define CMD_OVERRIDE_SPINDLE_COARSE_MINUS 0x9B
#define CMD_OVERRIDE_SPINDLE_FINE_PLUS 0x9C
#define CMD_OVERRIDE_SPINDLE_FINE_MINUS 0x9D
#define CMD_OVERRIDE_SPINDLE_STOP 0x9E
#define CMD_OVERRIDE_COOLANT_FLOOD_TOGGLE 'C'
#define CMD_OVERRIDE_COOLANT_MIST_TOGGLE 'M'
#define CMD_PID_REPORT 0xA2
#define CMD_TOOL_ACK 0xA3
#define CMD_PROBE_CONNECTED_TOGGLE 0xA4

#define JOGMODE_FAST '0'
#define JOGMODE_SLOW '1'
#define JOGMODE_STEP '2'
#define JOGMODE_CYCLE 'h'
#define JOGMODIFY_CYCLE 'm'

// The slave implements a 256 byte memory. To write a series of bytes, the master first
// writes the memory address, followed by the data. The address is automatically incremented
// for each byte transferred, looping back to 0 upon reaching the end. Reading is done
// sequentially from the current memory address.
#define I2C_TIMEOUT_VALUE 100000  //microseconds

// Alarm executor codes. Valid values (1-255). Zero is reserved.
typedef enum {
    Alarm_None = 0,
    Alarm_HardLimit = 1,
    Alarm_SoftLimit = 2,
    Alarm_AbortCycle = 3,
    Alarm_ProbeFailInitial = 4,
    Alarm_ProbeFailContact = 5,
    Alarm_HomingFailReset = 6,
    Alarm_HomingFailDoor = 7,
    Alarm_FailPulloff = 8,
    Alarm_HomingFailApproach = 9,
    Alarm_EStop = 10,
    Alarm_HomingRequried = 11,
    Alarm_LimitsEngaged = 12,
    Alarm_ProbeProtect = 13,
    Alarm_Spindle = 14,
    Alarm_HomingFailAutoSquaringApproach = 15,
    Alarm_SelftestFailed = 16,
    Alarm_MotorFault = 17,
    Alarm_AlarmMax = Alarm_MotorFault
} alarm_code_t;
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

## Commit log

2021-10-06 Initial commit of design files.
    [Change Log.SchDoc, I2C_Jog_Controller.PrjPCB, I2C_Jog_Controller.SchDoc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]
2021-11-16 Commit latest files.
    [I2C_Jog_Controller.PrjPCB]
2022-01-15 Commit A3 revisions, source code and mech.
    [10mm_button.SLDPRT, 10mm_button.STL, 4mm_button.SLDPRT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]
2022-01-20 Fixed some CAD issues.
    [TopCover.SLDPRT, jog_box.SLDASM]
2022-01-25 Commit updated PCB layout (switch to USB-C connector)
    [I2C_Keypad.SchDoc, I2C_Keypad_host_module.SchDoc]
2022-04-21 Commit A4 files and CAM
    [I2C_Jog_Controller.PrjPCB, I2C_Jog_Controller.SchDoc, I2C_Jog_Controller_CAM_OUTPUT_A4.csv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]
2022-04-21 Commit Readme images and doc.
    [I2C_Jog_Controller.PrjPCB]
2022-04-21 Commit updated button map.
2022-04-21 Corrected typos in Readme.md
    Couple of typos. No big deal.
    "Interfae" was is my favourite cybergoth band from the 90s
2022-05-11 Fixed BOM issue with LEDS.
    [I2C_Jog_Controller_CAM_OUTPUT_A4.csv, I2C_Jog_Controller_CAM_OUTPUT_A4.xlsx]
2022-05-11 Commit missing Q2 from BOM and PNP.
    [I2C_Jog_Controller_CAM_OUTPUT_A4.csv, I2C_Jog_Controller_CAM_OUTPUT_A4.xlsx]
2022-05-11 Commit latest design files.
    [I2C_Jog_Controller.SchDoc, I2C_Keypad_host_module.SchDoc]
2022-05-12 Commit R4 board step model.
2022-05-18 added count to STL filenames
    [10mm_button_x16.STL, 4mm_button_x2.STL, lightpipe_x3.STL]
2022-05-24 Fixed issue with extra cancel character being sent.
    [app_main.cpp]
2022-07-05 Initial import of MSLA buttons and enclosure.
    [4mm Button Short x2.stl, 4mm Button x2.stl, Buttom Enclosure - No Micro USB.stl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]
2022-07-06 Update README.md
    Fix number of heatset inserts required.
2022-07-13 Replace M3 screws and inserts on cover with M2.6 self tapping screws, and adjust clearances around resistor near I2C buffer. Update README to match.
    [Jog2k Deluxe Edition.step, Top Cover.stl]
2022-07-18 Fix variant issues.
    [I2C_Jog_Controller.PrjPCB, I2C_Jog_Controller.SchDoc, I2C_Keypad.SchDoc]
2022-08-01 Fix bottom enclosure filenames.
    [Bottom Enclosure - No Micro USB.stl, Bottom Enclosure - No Type C.stl, Bottom Enclosure.stl]
2022-08-13 Updated Jog2k buttons optimized for FDM printing.
    [Flood Button Cover.stl, Fn Button Cover.stl, Halt Button Cover.stl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]
2022-08-14 Minor STL updates.
    [Bottom Enclosure.stl, Mist Button Cover.stl, Override Button Core 6x.stl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]
2022-08-14 Corrected some fit issues.
    [Bottom Enclosure.stl, Top Cover 1.3in Display.stl]
2022-08-30 Moved kptsr off CC pin.
    [I2C_Jog_Controller.PrjPCB, I2C_Keypad.SchDoc, I2C_Keypad_host_module.SchDoc]
2022-09-02 Added a case for the button PCB
    [Button PCB Case Bottom.stl, Button PCB Case Cover.stl, Button PCB Case v2.f3d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]
2022-09-03 Changing the LED to another one
    The current LED in the BOM is only available in "standard" assembly, which is much higher cost.
    Switching to this new led in order to avoid the "standard" assembly
    Changelog :
    - switching led C2761795 to C2874885
    [I2C_Jog_Controller_CAM_OUTPUT_A4.xlsx]
2022-09-03 Edited to match folders to resin buttons.
    [D-Pad Upper.stl, Flood Button Cover.stl, Fn Button Cover.stl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]
2022-09-04 updated buttons.
    [Override Button Core 6x.stl, Override Button Solid 6x.stl, Small Button Lightpipe 6x.stl]
2022-09-04 added screen mounting and updated front face STLs.
    [ScreenSpacer.stl, Screenclip x3.stl, Top Cover 1.3in Display.stl]
2022-09-05 Update Top Cover 1.3in Display.stl
    [Top Cover 1.3in Display.stl]
2022-09-06 updated buttons, organized directories.
    [Jog2k Deluxe with FDM Buttons.f3d, Jog2k Deluxe with FDM Buttons.step, Large Button Lightpipe 5x.stl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]
2022-09-10 Commit updated A6 revision.
    [I2C_Jog_Controller.PrjPCB, I2C_Jog_Controller.SchDoc, I2C_Keypad.SchDoc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]
2022-09-10 Commit RP2040 page
    [RP2040_MCU.SchDoc]
2022-09-12 Updated A6 revision.
    [I2C_Jog_Controller.PrjPCB]
2022-09-13 Commit A5 build files.
    [I2C_Jog_Controller_CAM_OUTPUT_A4.xlsx, I2C_Jog_Controller_CAM_OUTPUT_A5.csv, I2C_Jog_Controller_CAM_OUTPUT_A5.xlsx]
2022-09-14 Added STLs for 1.3 inch screen.
    [Bottom Enclosure 1.3inch.stl, Display Retainer 1.3inch.stl, Top Cover 1.3inch.stl]
2022-10-01 Removed extraneous 1.3 inch stls.
    [Bottom Enclosure.stl, ScreenSpacer.stl, Screenclip.stl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]
2022-10-01 Commit A5 schematic PDF.
2022-10-02 Fix link for flat head screws.
2022-11-17 Commit minor component value updates.
    [I2C_Jog_Controller.PrjPCB, I2C_Keypad.SchDoc, I2C_Keypad_host_module.SchDoc]
2022-11-29 Commit build files and PDF schematic for A6. Commit updated mechanicals for Slim.
    [Bottom Enclosure_slim.STEP, I2C_Jog_Controller.PrjPCB, I2C_Jog_Controller_CAM_OUTPUT_A4.csv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]
2022-11-29 Remove A4 archive and rename current build archives.
2022-11-29 Commit board image.
2023-01-02 Uploaded correct STL for slim enclosure.
2023-01-22 Remove mechanical parts, which have been migrated to Mods & Accessories
    [10mm_button.SLDPRT, 10mm_button_x16.STL, 4mm Button Short x2.stl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]
2023-05-04 Fixed some minor issues with latest core plugin code. Still need to resolve status packet mismatch.
    [app_main.cpp, i2c_jogger.h]
2023-05-04 Fixed conflict with macro6 keycode.
    [app_main.cpp, i2c_jogger.h]
2024-01-01 Updated unlock and flip functions.
    [app_main.cpp, i2c_jogger.h]
2024-01-15 Commit update to fix issue with inverted Y axis.
    [app_main.cpp, i2c_jogger.h]
2024-12-21 commit fix for 4th axis jogging.
    [app_main.cpp, i2c_jogger.h]
2025-03-03 Add fine overrides for feed/speed and remap spindle macro to fan toggle
2025-03-15 More fixes for upstream plugin compatibility
    [app_main.cpp, i2c_jogger.h]
2025-03-15 Potential fix for using variable status packet length
    [app_main.cpp]
2025-03-18 Macro key remapping and 4th axis jog fixes
    [app_main.cpp, i2c_jogger.h]
2025-08-30 Macro fix and improved 3-axis handling
    [app_main.cpp]
2025-09-27 Revert primary spindle button behaviour to CMD_OVERRIDE_SPINDLE_STOP
    [app_main.cpp, i2c_jogger.h]
2026-02-20 Add GitHub Actions CI build and embed git SHA in firmware
    Add a GitHub Actions workflow that builds the firmware on every push
    and PR using pico-sdk 1.5.1. The built UF2 artifact is uploaded with
    the short git SHA in its filename for easy identification.
    The short git SHA is also injected at compile time via -DBUILD_SHA so
    the OLED boot splash displays the exact build (e.g. "v1.1.0+abc1234").
    Local builds without the flag show "v1.1.0+dev". The boot splash font
    is reduced to FONT_8x8 to accommodate the longer version string.
    [app_main.cpp, i2c_jogger.h]
2026-02-21 Fix for reporting updated alarm codes
    [app_main.cpp]
